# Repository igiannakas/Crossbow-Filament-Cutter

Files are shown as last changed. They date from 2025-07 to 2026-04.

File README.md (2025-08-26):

[][cc-by-nc-sa]

# Crossbow
### A CNC filament cutter from DW-Tas: <a href="https://ko-fi.com/O5O5OCC0K"> Ko-Fi</a>, <a href="https://github.com/DW-Tas">GitHub</a>

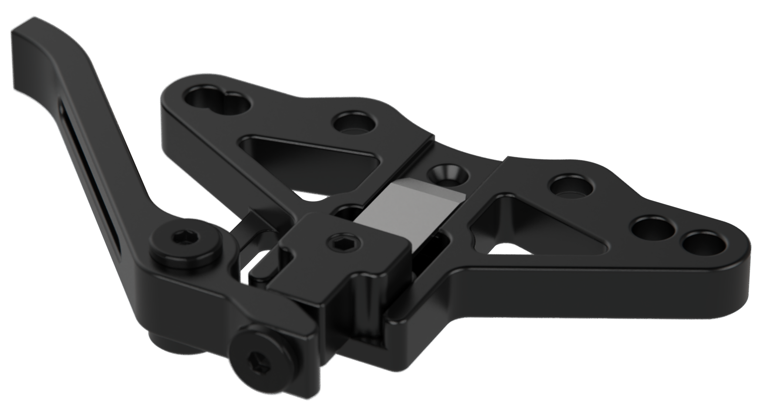
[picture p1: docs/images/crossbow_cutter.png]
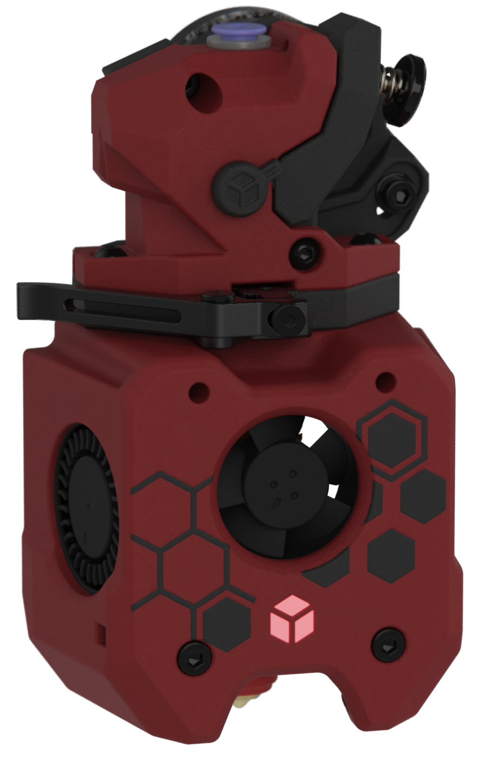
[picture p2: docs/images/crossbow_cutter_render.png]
<br/>

## Design philosophy
The crossbow filament cutter was developed to provide a robust, reliable, easily serviceable, versatile and universal filament cutting solution for printed toolheads. Key features include:
1. Aluminum CNC construction: Reliable cutting action that can withstand multi-thousand operations without wear.
2. Low profile and low mass: maintains toolhead rigidity, centre of mass and input shaper performance.
3. Ease of servicing: two easily accessible screws to remove and replace cutting blade and clean the filament path.

## Designed for the A4T, but intended for universal use
Crossbow was designed and developed around the A4T, but is intended for universal for use in printed toolheads that have a flat mounting surface below the extruder.<br/><br/>
Crossbow A4T parts can be downloaded here: <a href="https://github.com/Armchair-Heavy-Industries/A4T/tree/main/STL/Extruder%20Adapters/For%20Crossbow%20filament%20cutter">https://github.com/Armchair-Heavy-Industries/A4T</a>.
<br/><br/>

> [!TIP] 
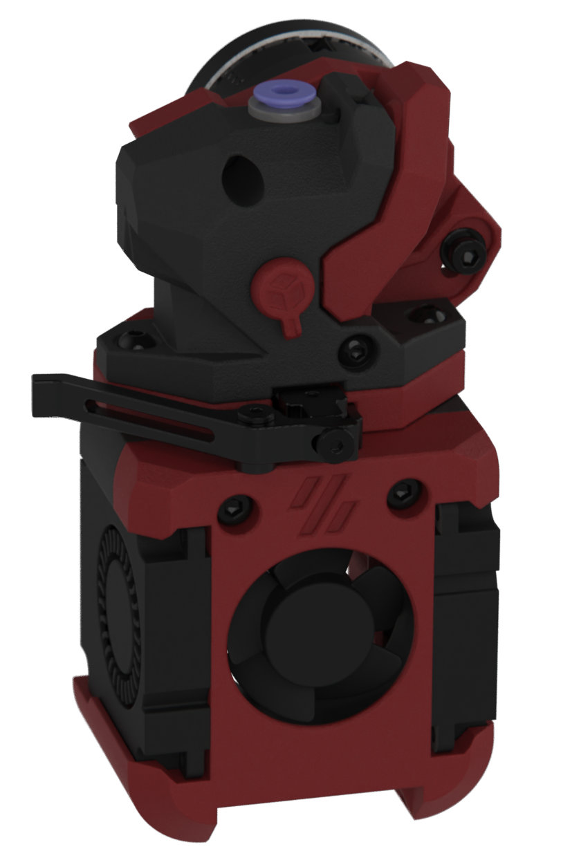
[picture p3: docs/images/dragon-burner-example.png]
> The design accomodates extruders that use the Sherpa-Mini or Oribiter v2.0 mounting hole spacing (Checked for fit with Dragon Burner in CAD models with an example Dragon Burner Mod included in the [Dragon Burner example](<Dragon Burner example>) folder).<br/><br/>

## Blade replacement
Blade replacement is generally recomended after 3000-4000 cuts, depending on the material being cut. Crossbow can use a #17A or #4 hobby knife blade. Trimming the blades to size is required. The following jig is available to help cut the blade down.

**Jig BOM:**
1. 4x M3x8 SHCS / BHCS screws
2. 4x M3 Square Nuts (DIN 562)
3. #17 or #4 hobby knife blade
4. Printed jig parts: [Blade cutting and alignment jig.stl](<STL/Blade cutting and alignment jig.stl>)

**Instructions video:**<br/>
[](https://www.youtube.com/embed/HI4ksrRDHjI)

<br/><br/>

## Screw adjustment

> [!WARNING] 
> The two main screws that act as pivots should have medium thread locking compound applied.

* **Lever Arm Pivot:** Tighten the screw to allow smooth movement of the lever arm during cutting, while preventing vertical play or rattling.
* **Blade Holder Pivot:** Start with the screw too loose then tighten the screw until the blade begins to shift slightly toward the filament path during its cutting motion. This ensures full travel of the cutting arm and minimizes unwanted movement.

<br/><br/>

## Licenced manufacturers
Crossbow is being manufactured under license by:<br/><br/>
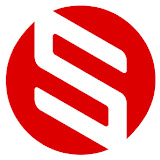
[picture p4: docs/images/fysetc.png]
Fysetc
<a href="https://aliexpress.com/store/3480083"><br/>Fysetc AliExpress Store</a>
<br/>
Buy it now: 
* <a href="https://www.fysetc.com/products/fysetc-cnc-crossbow-filament-cutter-used-for-printed-toolheads-compatible-with-a4t-sherpa-mini-oribiter-v2-0-dragon-burner">Fysetc Website</a>
* <a href="https://aliexpress.com/item/1005009769281594.html">AliExpress</a>
<br/><br/>
> [!TIP] 
> ### You can help support the development of this project.<br/>
> Donate at https://ko-fi.com/dwtas<br/>
ko-fi (https://ko-fi.com/dwtas)
<br/><br/>

### Credits
* Inspired by Treintjes' <a href="https://github.com/Treintjes/Magneto_Filament_Cutter">Magneto_Filament_Cutter</a><br/><br/>
* Beta testers
  * igiannakas <a href="https://github.com/igiannakas/">GitHub</a>
  * KnightRadiant <a href="https://github.com/jrlomas/">GitHub</a>
  * jeremytodd1
  * jbob
<br/><br/>
#### This work is licensed under a
[Creative Commons Attribution-NonCommercial-ShareAlike 4.0 International License][cc-by-nc-sa].

[][cc-by-nc-sa]

[cc-by-nc-sa]: http://creativecommons.org/licenses/by-nc-sa/4.0/
[cc-by-nc-sa-image]: https://licensebuttons.net/l/by-nc-sa/4.0/88x31.png
[cc-by-nc-sa-shield]: https://img.shields.io/badge/License-CC%20BY--NC--SA%204.0-lightgrey.svg

### License clarification regarding non-commercial use:
The non-commercial aspect of this license is for cases where Crossbow is the product, not the use of Crossbow to create products.<br/>
I.e. If you wish to sell Crossbow as a product, you would need to seek a commercial license before doing so. </br>
It is NOT intended to prevent the use of Crossbow in a printer that you use to provide commercial services. If you want to run Crossbow as a toolhead for your print farm printers, go right ahead.

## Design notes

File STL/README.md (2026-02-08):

### STLs for printed parts for A4T are maintained on the A4T Repo

[A4T Extruder Adapters for Crossbow](https://github.com/Armchair-Heavy-Industries/A4T/tree/main/STL/Extruder%20Adapters/For%20Crossbow%20filament%20cutter)

[A4T Configurator](https://a4t.wizards-enclave.net/)

#### Depressor Arms configuration options:
There are three depressor arm configuration options included in this repo: 
1. Standard Voron gantry (used with both with and without gantry backers).
2. Monolith gantry
3. Siboor Trident 9MM gantry

#### Depressor Arms BOM:
**Standard Voron Gantry (no backers) and Monolith Gantry versions**
- 2x M3x10 BHCS to fix the depressor arm base to the gantry
- 2x M3x14-M3x18 BHCS to fix the depressor arm to the depressor base
- 2x M3x5x5 heatsets (standard voron spec). Fit from the rear of the depressor arm base.
- 2x M3 washers for the depressor base

**Standard Voron Gantry (with backers)**
- 2x M3x12 BHCS to fix the depressor arm base to the gantry
- 2x M3x14-M3x18 BHCS to fix the depressor arm to the depressor base
- 2x M3x5x5 heatsets (standard voron spec). Fit from the rear of the depressor arm base.
- 2x M3 washers for the depressor base
<br/>

<table>
  <tr>
    <td align="center" width="33%">
      <b>Standard Gantry</b><br/><br/>
      
    </td>
    <td align="center" width="33%">
      <b>Standard Gantry with backers</b><br/><br/>
      
    </td>
    <td align="center" width="33%">
      <b>Monolith Gantry</b><br/><br/>
      
    </td>
  </tr>
</table>

<br/><br/><br/><br/>

#### Sources and attribution
Standard Depressor Arm Base [Standard and Monolith Gantry].stl is derived from the A4T-AFC repository (https://github.com/SouthAsh1/A4T-AFC/tree/main)<br/><br/>
Depressor Arm [Standard Voron Gantry].stl is a shortened version from the same place modifed to work with Crossbow Cutter on a standard Voron gantry.<br/><br/>
Depressor Arm [Monolith Gantry].stl is a shortened version from the same place modifed to work with Crossbow Cutter on the monolith 2WD and AWD gantry.<br/><br/>

<br/><br/><br/><br/>

> [!NOTE] 
> Aslo included in this folder is an example mod for Dragon Burner standard cowl.

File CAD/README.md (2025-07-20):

[][cc-by-nc-sa]

# Temporary Integration CAD

<br/> 
Full CAD and drawings will be uploaded once tested.<br/><br/>
For now, here is an integration model to help plan integration with other toolheads.

[A4T CNC Filament Cutter - Integration CAD.step](<A4T CNC Filament Cutter - Integration CAD.step>)

<br/><br/><br/>
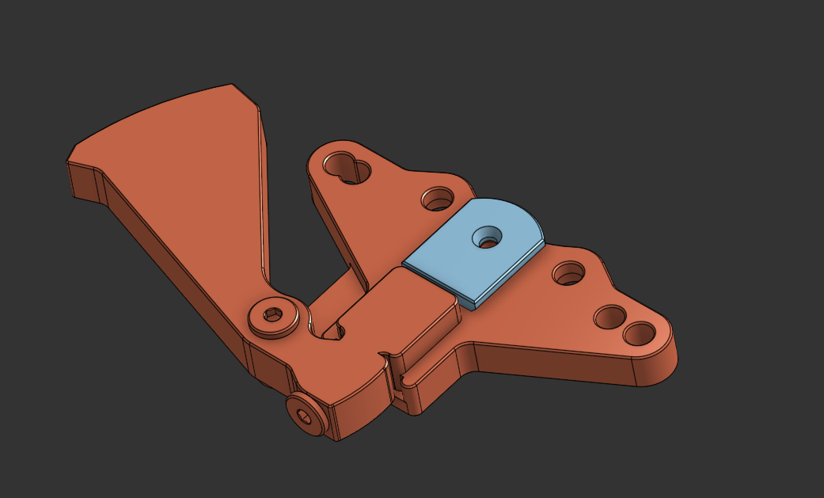
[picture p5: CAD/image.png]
Integration Model

<br/><br/><br/>

#### This work is licensed under a
[Creative Commons Attribution-NonCommercial-ShareAlike 4.0 International License][cc-by-nc-sa].

[][cc-by-nc-sa]

[cc-by-nc-sa]: http://creativecommons.org/licenses/by-nc-sa/4.0/
[cc-by-nc-sa-image]: https://licensebuttons.net/l/by-nc-sa/4.0/88x31.png
[cc-by-nc-sa-shield]: https://img.shields.io/badge/License-CC%20BY--NC--SA%204.0-lightgrey.svg

### License clarification regarding non-commercial use:
The non-commercial aspect of this license is for cases where A4T Cutter is the product, not the use of A4T Cutter to create products.<br/>
I.e. If you wish to sell A4T Cutter as a product, you would need to seek a commercial license before doing so. </br>
It is NOT intended to prevent the use of A4T Cutter in a printer that you use to provide commercial services. If you want to run A4T Cutter as a toolhead for your print farm printers, go right ahead.

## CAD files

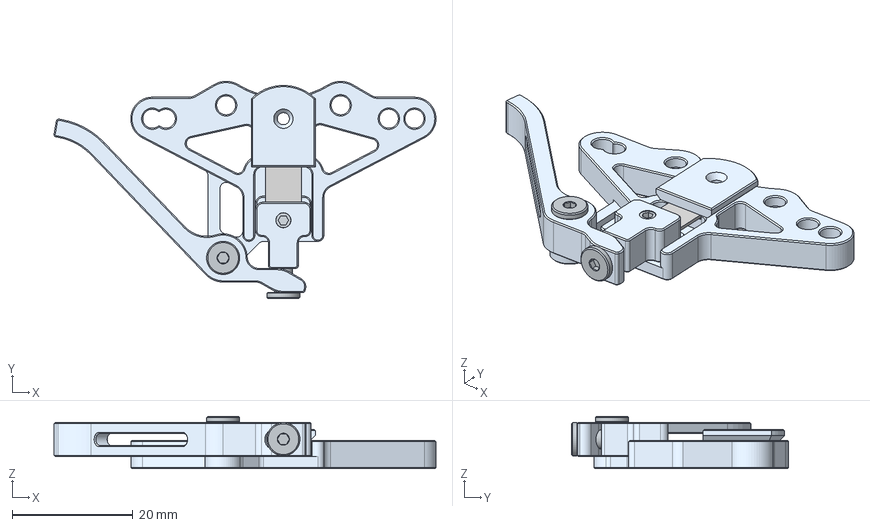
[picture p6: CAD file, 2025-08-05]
CAD/Crossbow CNC filament cutter assembly.step
63.4 x 36.0 x 8.70 mm
Crossbow - Blade caddy
M3x6 Ultra low profile socket head screw
Crossbow - Main Body
Flat point hex socket set screw M3x0.5 x 3
17A cut down blade
Crossbow - Lever
M3x8 Ultra low profile socket head screw
Crossbow - Top Cap
Magnet 6x1.5 x 2

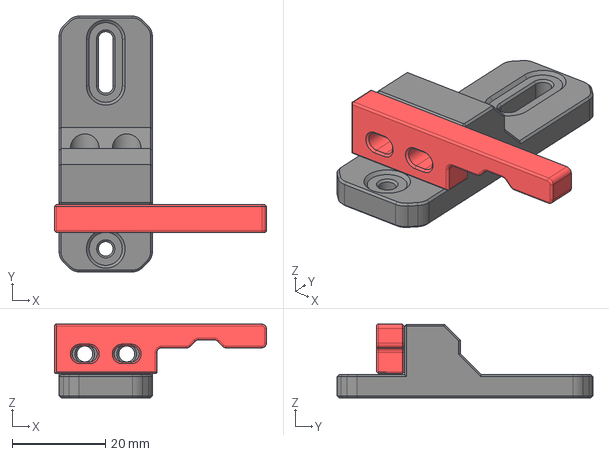
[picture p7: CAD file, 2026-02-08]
CAD/Crossbow Depressor Arm and Holder [Monolith Gantry].step
45.5 x 54.9 x 15.8 mm
Depressor Arm Base
Depressor Arm

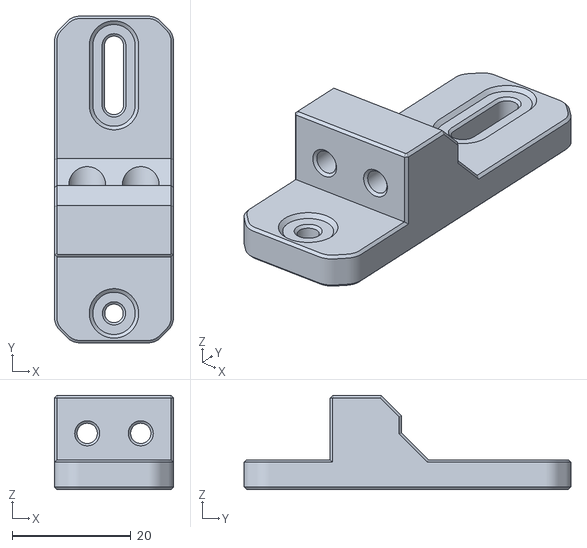
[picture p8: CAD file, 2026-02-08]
STL/Depressor Assemblies/Depressor Arm Base [Monolith Gantry].stl
20.0 x 54.9 x 15.8

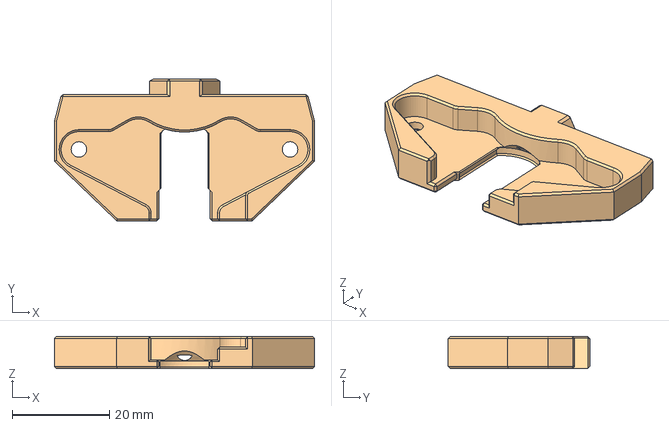
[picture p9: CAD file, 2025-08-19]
STL/Dragon Burner example/Crossbow cutter holder - WW-BMG (Sherpa-Mini spacing) - Dragon Burner.step
53.6 x 29.2 x 6.60 mm

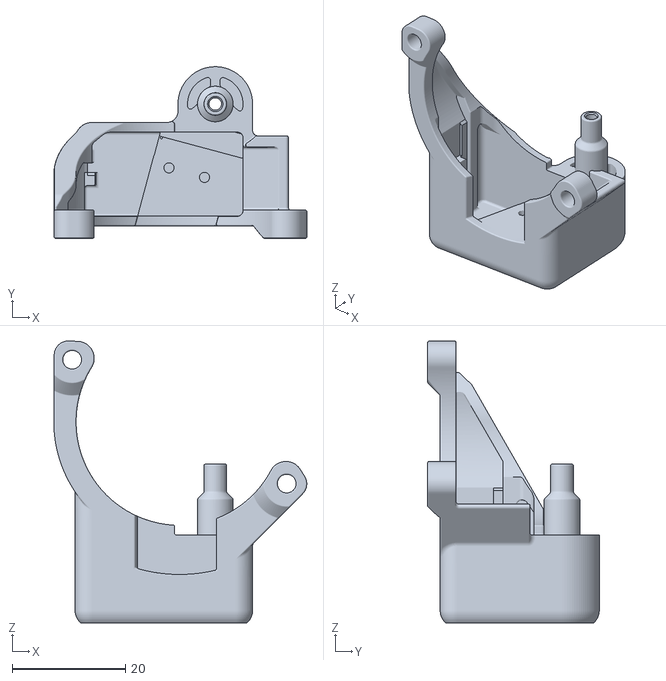
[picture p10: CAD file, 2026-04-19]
User_Mods/Orbiter_filament_guide/STL/Orbiter Filament Guide.stl
44.7 x 30.3 x 49.9

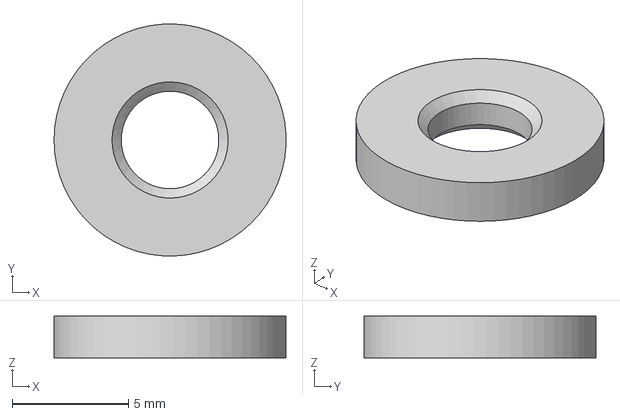
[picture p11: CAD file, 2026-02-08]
CAD/PTFE tube cutter jig.step
9.99 x 10.00 x 1.80 mm

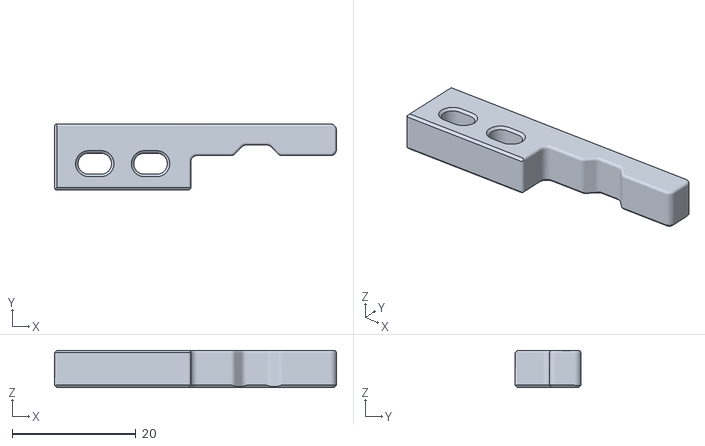
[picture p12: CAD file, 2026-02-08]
STL/Depressor Assemblies/Depressor Arm [Monolith Gantry].stl
45.5 x 10.7 x 6.05

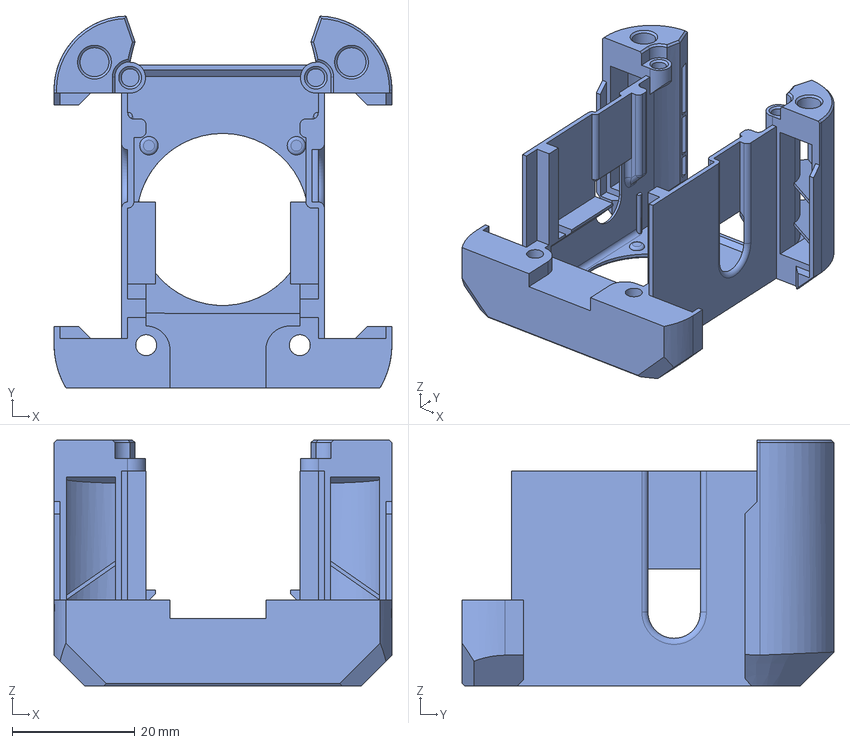
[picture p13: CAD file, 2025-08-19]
STL/Dragon Burner example/Dragon Burner v8 Standard Cowl for Crossbow.step
55.0 x 60.5 x 40.0 mm

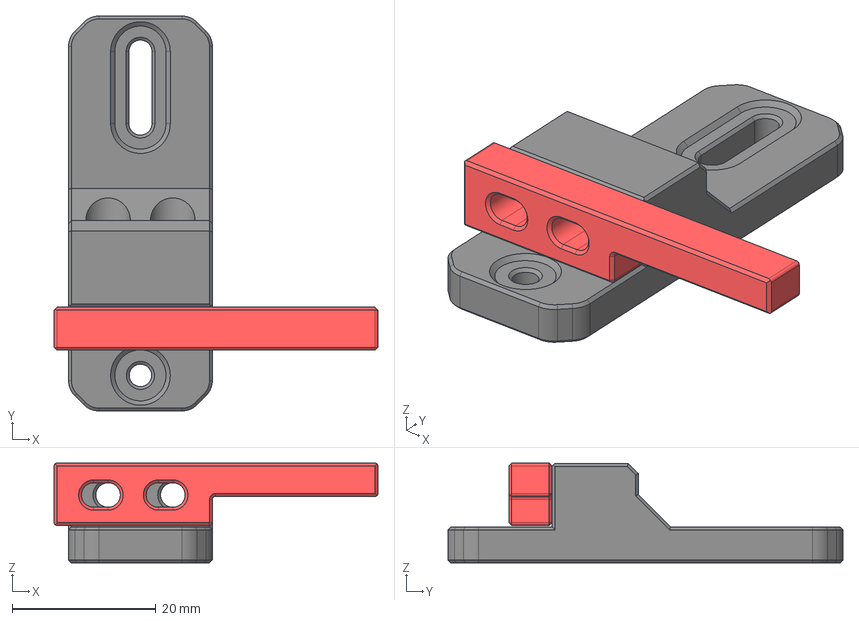
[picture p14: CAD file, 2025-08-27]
CAD/Crossbow Depressor Arm and Holder [Standard Voron Gantry].step
45.0 x 54.9 x 13.9 mm
Depressor Arm Base
Depressor Arm

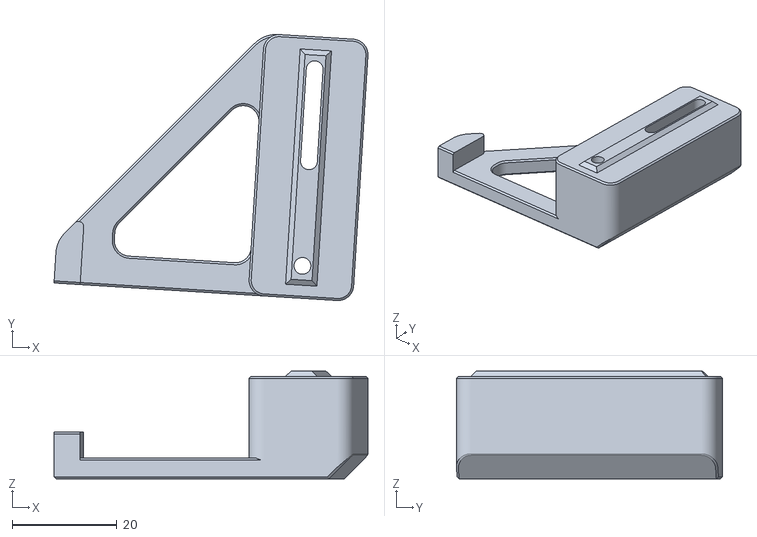
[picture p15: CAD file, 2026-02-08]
STL/Depressor Assemblies/Depressor [Siboor trident 9mm].stl
59.9 x 50.8 x 20.6

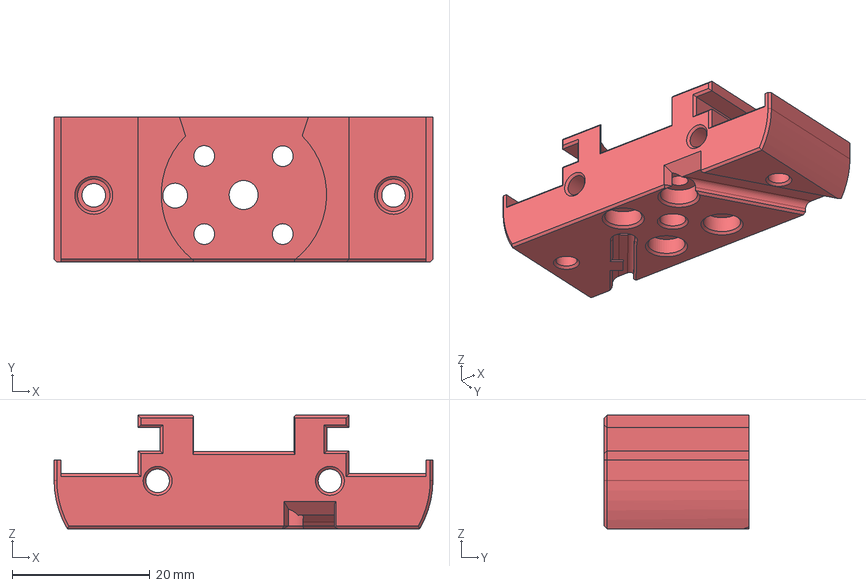
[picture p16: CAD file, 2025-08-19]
STL/Dragon Burner example/Dragon_Burner_v0.2_v8 parts - Dragon_Ace_HF_Mount.step
55.0 x 21.0 x 16.5 mm

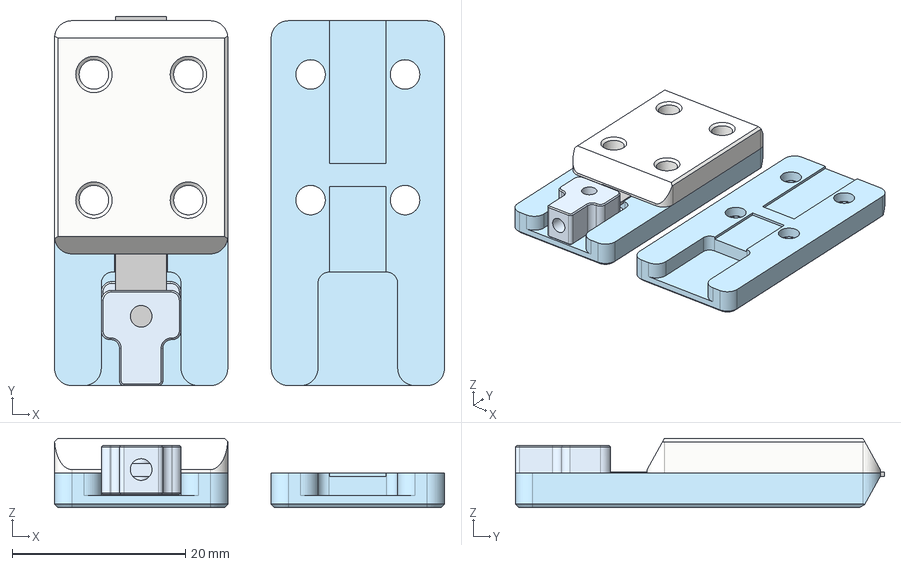
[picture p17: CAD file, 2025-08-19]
CAD/Blade cutting and alignment jig.step
45.0 x 42.6 x 8.00 mm
A4T Filament Cutter - Blade caddy
17A cut down blade x 2

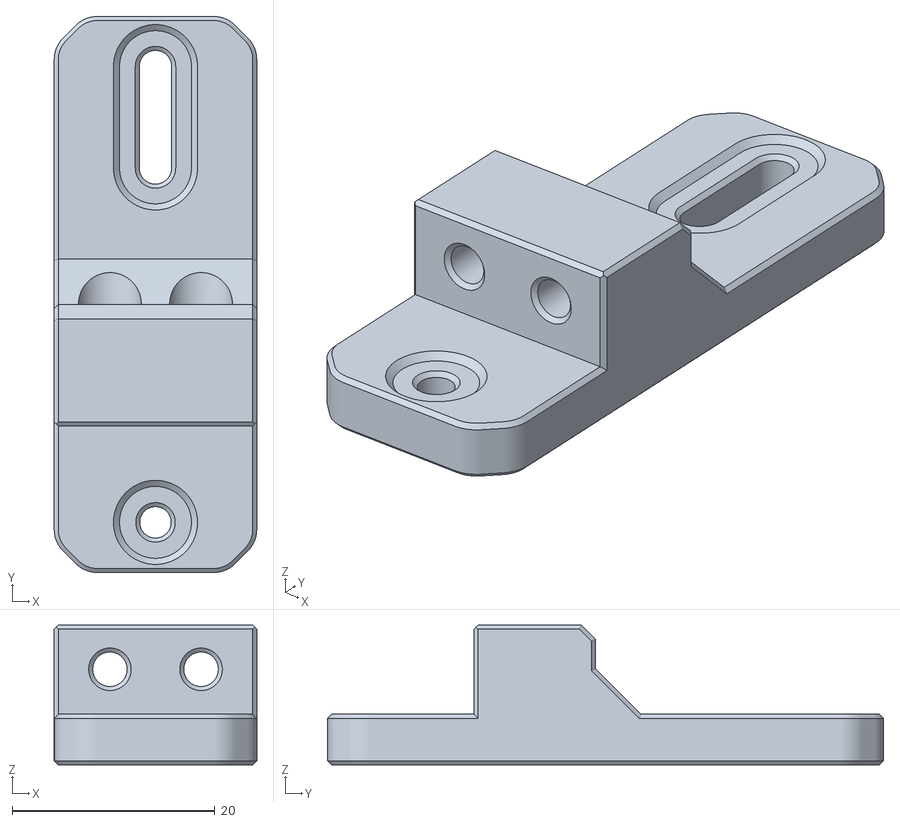
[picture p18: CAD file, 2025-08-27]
STL/Depressor Assemblies/Depressor Arm Base [Standard Gantry].stl
20.0 x 54.9 x 13.8

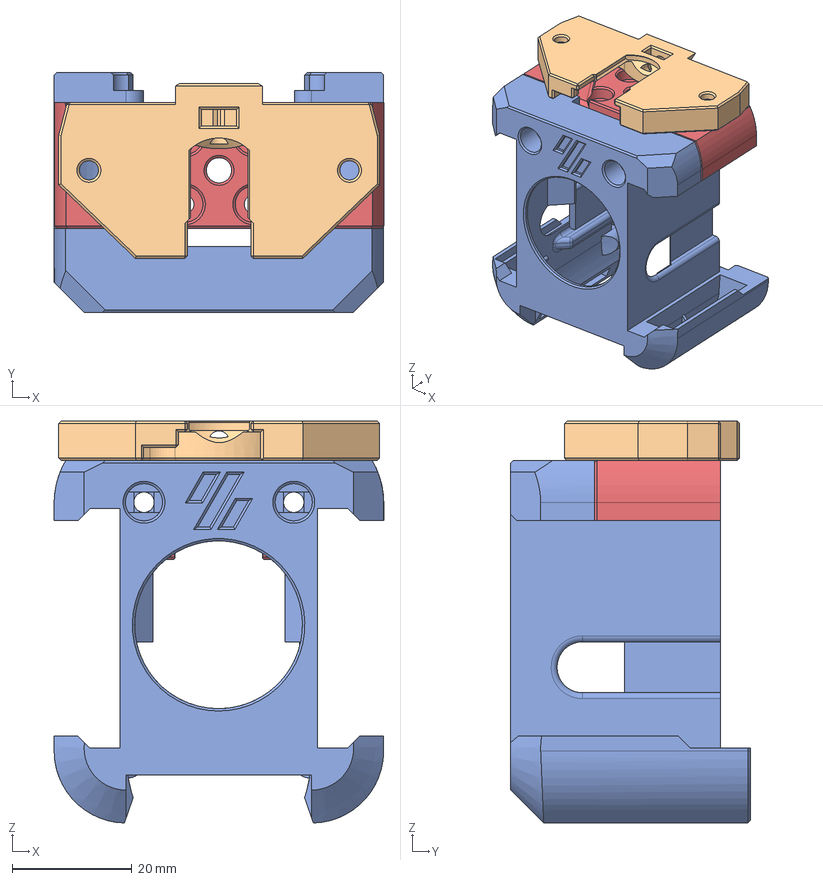
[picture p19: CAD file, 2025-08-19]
STL/Dragon Burner example/Dragon_Burner_v0.2_v8 for Crossbow.step
55.0 x 40.0 x 67.1 mm
Standard
Crossbow cutter holder - WW-BMG (Sherpa-Mini spacing)
Dragon_Ace_HF_Mount

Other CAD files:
CAD/Crossbow integration CAD.step
STL/Depressor Assemblies/Depressor Arm [Standard Voron Gantry].stl
STL/Blade cutting and alignment jig.stl
STL/Dragon Burner example/Crossbow cutter holder - WW-BMG (Sherpa-Mini spacing) - Dragon Burner.stl
STL/Dragon Burner example/Dragon Burner v8 Standard Cowl for Crossbow.stl
STL/Dragon Burner example/Dragon_Burner_v0.2_v8 parts - Dragon_Ace_HF_Mount.stl
STL/PTFE tube cutter jig.stl

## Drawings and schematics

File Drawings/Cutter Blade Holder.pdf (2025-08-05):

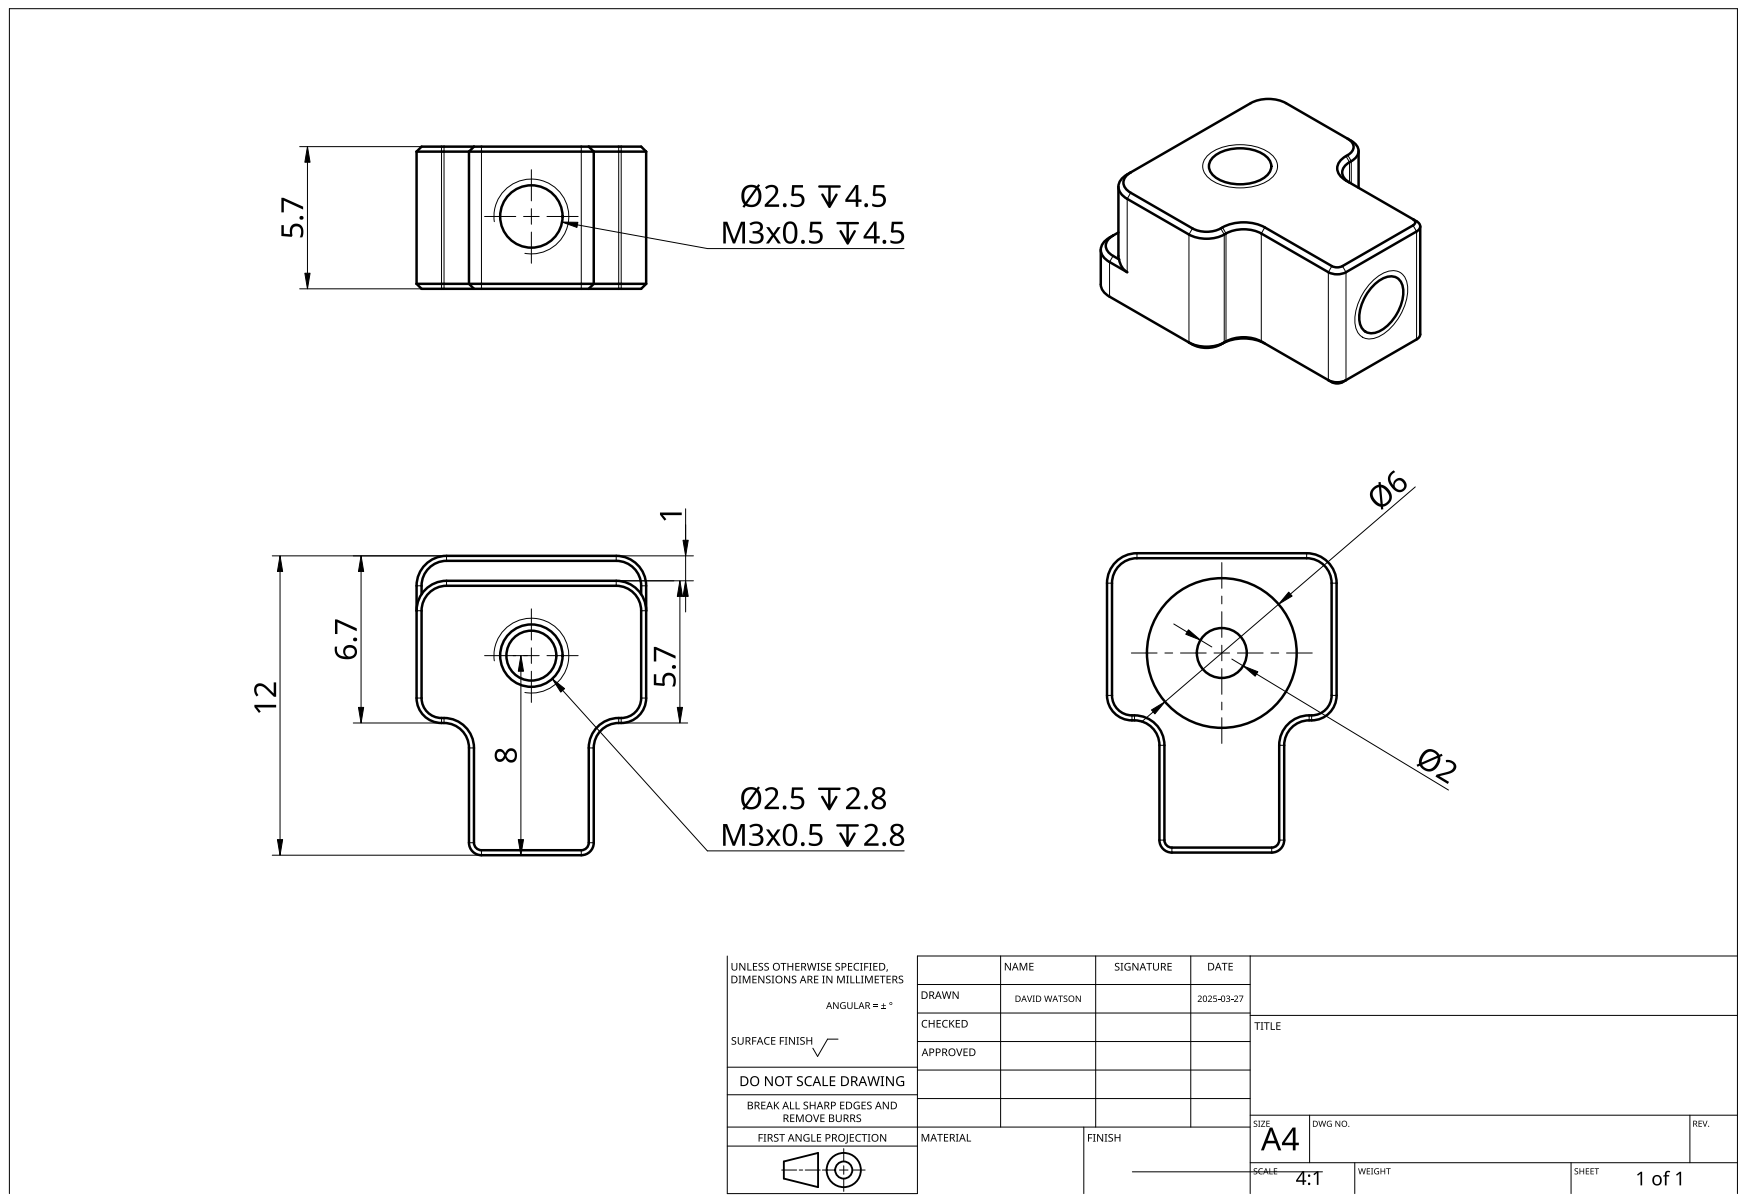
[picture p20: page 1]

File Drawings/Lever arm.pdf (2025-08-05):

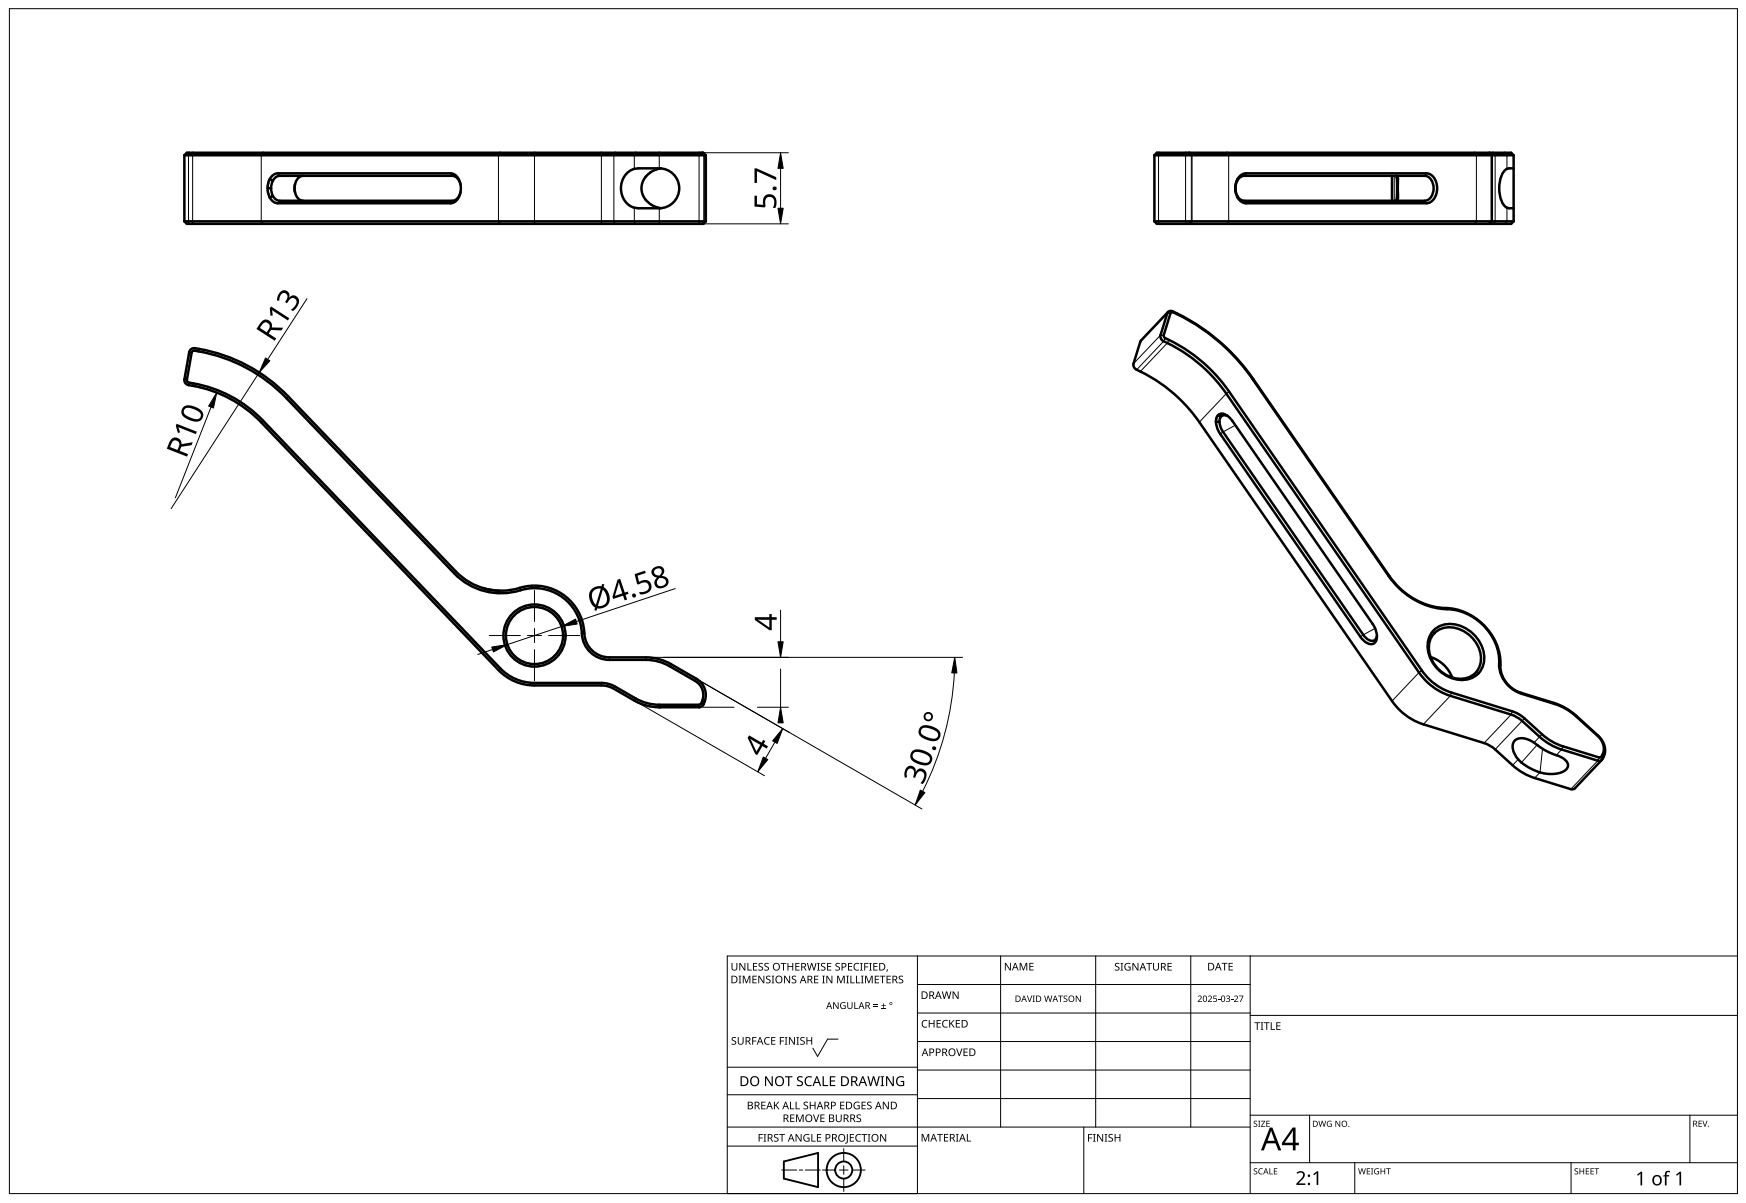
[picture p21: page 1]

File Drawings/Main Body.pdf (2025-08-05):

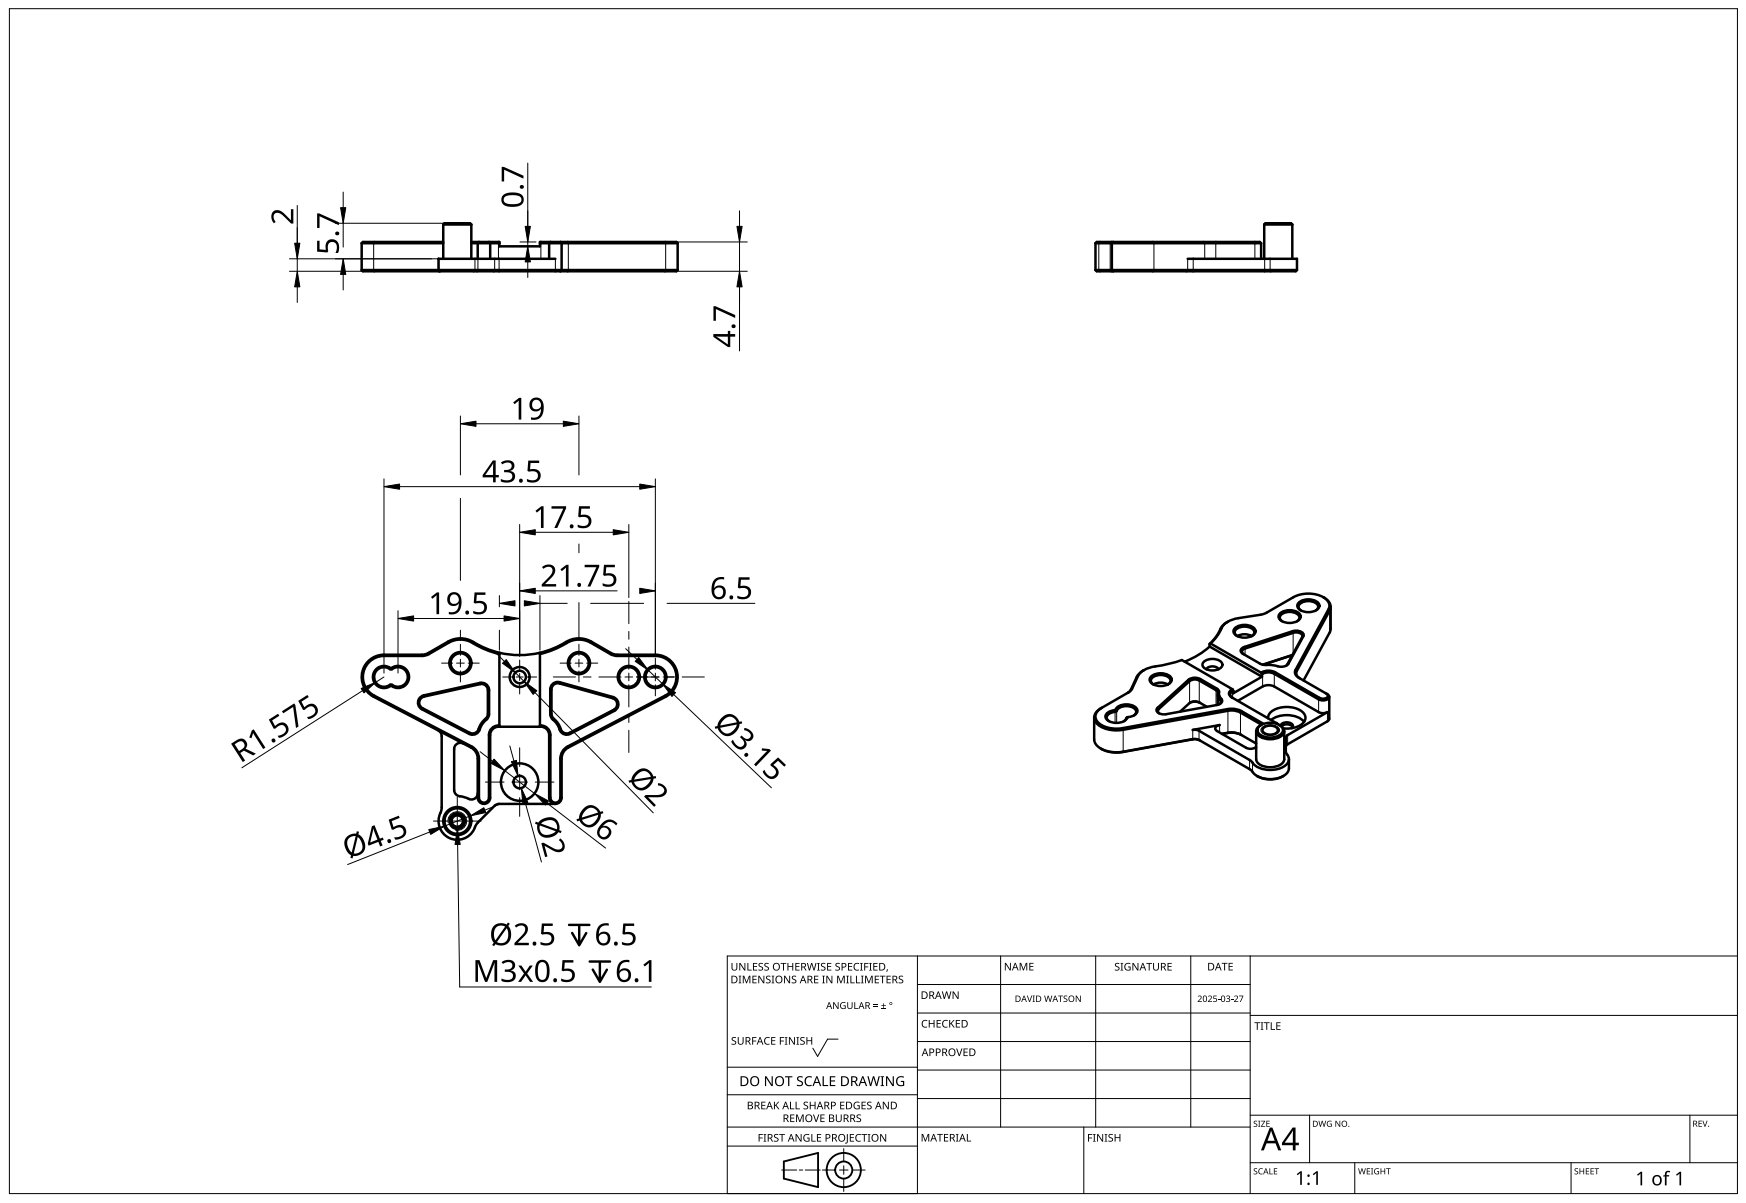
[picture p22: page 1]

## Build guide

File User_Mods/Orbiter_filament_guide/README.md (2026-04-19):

# Orbiter filament guide

To reduce chance of loading failure due to filament snagging on the entry of an Orbiter extruder.
<br/><br/>
Mod created by pajtaz

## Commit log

2025-07-20 upload integration model
    [A4T CNC Filament Cutter - Integration CAD.step]
2025-08-05 release upload
    [A4T CNC Filament Cutter - Integration CAD.step, Crossbow CNC filament cutter assembly.step, Crossbow integration CAD.step]
2025-08-19 upload example dragon burner files
    [Crossbow cutter holder - WW-BMG (Sherpa-Mini spacing) - Dragon Burner.step, Crossbow cutter holder - WW-BMG (Sherpa-Mini spacing) - Dragon Burner.stl, Dragon B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]
2025-08-19 readme updates and support files (depressor and blade jig)
    [Blade cutting and alignment jig.step, Blade cutting and alignment jig.stl, Crossbow cutter holder - WW-BMG (Sherpa-Mini spacing) - Dragon Burner.step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]
2025-08-26 add screw adjustment notes to readme
2025-08-27 Gantry mount and pin
    [Crossbow Gantry Pin and Holder.step, Depressor Arm Base.stl, Depressor Arm.stl]
2025-08-27 Depressor arm and base (#1)
    * Gantry mount and pin
    * Gantry mount and pin
    [Crossbow Gantry Pin and Holder.step, Depressor Arm Base.stl, Depressor Arm.stl]
2026-01-04 added depressor for siboor 9mm trident gantry
    [Depressor [Siboor trident 9mm].stl]
2026-01-08 Add a jig for cutting PTFE tube (#4)
    * Add a jig for cutting PTFE tube
    A simple jig to help with cutting the ptfe tube that protrudes from the toolhead cowling
    - 1.8mm height : as crossbow cutter ptfe hole is 1.7mm
    - 4.2mm inner diameter
    - 10mm outer diameter
    * Add chamfer of 0.4mm to inner circle
    [PTFE tube cutter jig.step, PTFE tube cutter jig.stl]
2026-02-08 Publish Monolith Gantry depressor arm. Reorg files for better organisation. Added depressor assembly images
    [Crossbow Depressor Arm and Holder [Monolith Gantry].step, Crossbow Depressor Arm and Holder [Standard Voron Gantry].step, Depressor Arm Base [Monolith Gantry].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]
2026-02-08 Publish Monolith Gantry depressor arm and QOL improvements to the depressor pages (#5)
    * Publish Monolith Gantry depressor arm. Reorg files for better organisation. Added depressor assembly images
    * Update README.md
    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
    [Crossbow Depressor Arm and Holder [Monolith Gantry].step, Crossbow Depressor Arm and Holder [Standard Voron Gantry].step, Depressor Arm Base [Monolith Gantry].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]
2026-04-19 Orbiter filament entry user mod
    [Orbiter Filament Guide.stl]

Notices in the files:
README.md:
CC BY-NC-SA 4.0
